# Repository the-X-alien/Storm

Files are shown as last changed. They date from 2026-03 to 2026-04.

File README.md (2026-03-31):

# Storm | A DIY 3D Printer



An open-source Cartesian bedslinger 3D printer built and designed from scratch to beat the Bambu Lab A1 in speed and print quality, by a 13 year old

Most budget 3D printers sacrifice speed for price or quality. Storm is better because it focuses on all three, fast, high quality, and affordability

I used a big Cartesian bedslinger structure + Klipper input shaping + high quality components.

## Goals
- 300–400mm/s print speeds, sub-5min Benchy
- Beat the Bambu Lab A1 in speed and quality
- Under $350 total including shipping and taxes
- Open source
- Screen
- Klipper Firmware
- Cool

## Specs
- Motion system: Cartesian bedslinger
- Build volume 220×220×300mm
- Firmware: Klipper
- Extruder: Sherpa Mini
- Hotend: TZ V6
- Probe: 3DTouch
- MCU: BTT SKR Mini E3 V3.0
- Raspberry Pi Zero 2W
- Display: ILI9341 2.8" SPI touchscreen
- Part Cooling: Dual 5015 blower fans 24V
- Hotend cooling: 4010 axial fan 24V
- Bed: 235×235mm 24V aluminum heated bed (Ender 3 bed) + PEI textured build plate

## Frame
- 4× 2040 aluminum extrusion 350mm for the base
- 2× 2020 aluminum extrusion 350mm for the Z towers
- 1× 2020 aluminum extrusion 350mm for the top crossbar

## Motion
- 8mm smooth linear rods on all axes (X, Y, Z) rails are too expensive :(
- LM8UU linear bearings
- T8 leadscrews 330mm for Z axis
- GT2 6mm belt for X and Y
  
## BOM
https://docs.google.com/spreadsheets/d/1btD1Bjle54Zft8ynW4hvl1bNV1Zsg6aF89J3ntGE-do/edit?usp=sharing

Total: ~$315 before tax and ~$347 with tax

## CAD
assembly in Onshape:
https://cad.onshape.com/documents/37467ea71eb1fca5838973f8/w/7266e1215341462849f7532b/e/d342240afd8f3da62d0e4bb2

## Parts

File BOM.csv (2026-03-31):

Part | Qty Needed | Total Cost | Why? | Anything Else? | Link
2040 T-slot extrusion 350mm | 4 | $27.00 | For base of the frame | Clear Anodize | HFS5-2040-350 | https://us.misumi-ec.com/vona2/detail/110302684350/?HissuCode=HFS5-2040-350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
2020 T-slot extrusion 350mm | 3 | $17.31 | For the X Axis and the two Z towers | Clear Anodize | HFS5-2020-350 | https://us.misumi-ec.com/vona2/detail/110302683830/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
M5 T-Nut Kit | 1 | $4.92 | To join parts | It has 100Pcs | https://www.aliexpress.us/item/3256808597854176.html?curPageLogUid=Rnu7snFro4kU
M5 8mm Bolt Kit | 1 | $4.99 | To screw into the T Nuts | It has 100Pcs | https://www.amazon.com/Stainless-Threaded-Spanner-Furniture-Fixture/dp/B0FPG1VZYH?s=hi
8mm smooth rod 350mm | 6 | $28.74 | For Y Guiding For the Bed and For Z Guiding For the Linear Rail | 6Pcs 8mm x 350mm | https://www.aliexpress.us/item/3256807362660070.html?mp=1
LM8UU linear bearing | 12 | $6.32 | 2 per rod, slides along smooth rod | 10Pcs | https://www.amazon.com/Bearings-Diameter-Bushing-Engraving-Projects/dp/B0GCKMDYPG?s=bazaar&srs=121974693011
T8 leadscrew 330mm | 2 | $9.54 | For Z Movement for the Linear Rail | 2Pcs 330mm Lead 8mm with nut | https://www.aliexpress.us/item/3256805992640426.html?src=google
5mm to 8mm flexible shaft coupler | 2 | $3.94 | Z motor to leadscrew | 5mm x 8mm | https://www.aliexpress.us/item/3256807100994003.html?src=google
GT2 6mm open belt | 1 | $3.90 | To move X and Y | White 5M | https://www.aliexpress.us/item/3256805175395061.html?mp=1
20T GT2 pulley 5mm bore | 4 | $3.96 | On X and Y motor shafts | 20 Teeth 5mm | https://www.temu.com/goods.html?goods_id=601099817656513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
GT2 5mm smooth idler pulley | 4 | $6.78 | Belt routing and tensioning | 5Pcs 20T W6 B5 Without Teeth | https://www.aliexpress.us/item/3256806303110250.html?curPageLogUid=b8VNkbBWfE8c
Nema17 Stepper Motor 17HS4401 | 1 | $0.99 | Y |  | https://www.aliexpress.us/item/3256808273084374.html?mp=1
Nema 17 Stepper Motor 42HS34 | 3 | $17.88 | X, 2x Z |  | https://www.aliexpress.us/item/3256805095424554.html?mp=1
Sherpa Mini Extruder | 1 | $17.55 | Extruder |  | https://www.aliexpress.us/item/3256804374952371.html?src=google
TZ V6 Hotend | 1 | $7.46 | Hotend | TZ V6 | https://www.aliexpress.us/item/3256808497028944.html?curPageLogUid=79nhbArLE8BA
Dual 5015 Blower Fans | 2 | $4.79 | Fans | 2pcs 24v Sleeve 4500RPM | https://www.aliexpress.us/item/3256807420529511.html?mp=1
4010 Axial Fan | 1 | $3.84 | Fan |  | https://www.aliexpress.us/item/3256806505312112.html?curPageLogUid=f7DXmx63Z9Cv
PTFE tube 1m | 1 | $2.35 | Filament Tube | 1m | https://www.aliexpress.us/item/3256807604679758.html?curPageLogUid=zfQeqruhbkQQ
Heated Bed | 1 | $21.59 | 235mm Heated Bed |  | https://www.amazon.com/Ender-V2-Heated-Bed-Replacement/dp/B08VHTW8CQ
235mm PEI Build Plate | 1 | $7.94 | 235mm Build Plate |  | https://www.aliexpress.us/item/3256808391943560.html?curPageLogUid=n9RwhLDzKk6A
Silicone bed leveling mounts | 4 | $2.67 | Attaches Bed to Bed Carridge | 4pcs | https://www.aliexpress.us/item/3256809017739961.html?curPageLogUid=N3SoxEZlCpfR
BTT SKR MINI E3 V3.0 | 1 | $27.60 | MCU |  | https://www.aliexpress.us/item/3256808846534149.html?mp=1
3DTouch | 1 | $7.39 | 3D Touch |  | https://www.aliexpress.us/item/3256805422565595.html?mp=1
Raspberry Pi 0 2W | 1 | $0.00 | Running Klipper Firmware | I have one already
ILI9341 2.8" SPI touchscreen | 1 | $0.00 | Touchscreen to control the printer | I have one already
DC 24V 15A 360W PSU | 1 | $17.98 | Power Supply | 24V 15A 360W | https://www.amazon.com/gp/product/B0146IAXYO/ref=ewc_pr_img_1?smid=A3R1K2GDMNRTEL&psc=1
LM2596S DC-DC Buck Converter | 1 | $0.00 | Power Supply For the Pi | I have one already
ADXL345 accelerometer module | 1 | $0.00 | Input Shaping | I have one already
Mechanical endstop limit switch | 3 | $4.59 | To know the end of the axis |  | https://www.amazon.com/MXRS-Hinge-Momentary-Button-Switch/dp/B088W8WMTB?s=bazaar&srs=121974693011
20awg Silicone Electrical Wire Cable | 1 | $9.98 | Wires | 6 Colors, 20 AWG | https://www.amazon.com/Electrical-Gauge-Silicone-Cable-Black/dp/B08QVKJPZP?s=bazaar&srs=121974693011
16AWG silicone wire | 1 | $7.99 | Wires for the Bed |  | https://www.amazon.com/Silicone-Electrical-Cable%EF%BC%8810ft-Temperature-Resistant/dp/B0D93K21TN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
M3 Screws and Nuts Assortment | 1 | $7.20 | Screws for everything besides the frame and joints |  | https://www.amazon.com/Button-Socket-Assortment-Strength-Appliance/dp/B0F9Y9WQVV?s=bazaar&srs=121974693011
8MM M3 Screws | 1 | $4.76 | Because I will need more than the 20 in the kit |  | https://www.amazon.com/720pcs-Assorted-Plastic-Furniture-Machinery/dp/B0GCLG1ZYB?s=bazaar&srs=121974693011
M3 Heat Set Inserts | 1 | $4.13 | Heat Set Inserts |  | https://www.amazon.com/Threaded-Inserts-Embedment-Printing-Automotive/dp/B0DNVZPX2B?s=bazaar&srs=121974693011
Inlet Module Plug Socket | 1 | $6.29 | The power switch and adapter for the psu |  | https://www.amazon.com/button-Adapter-Connector-Socket-MXRS/dp/B082ZFRV1B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
NEMA 5-15P to IEC320 C13 Power Cord | 1 | $2.79 | To plug into the wall |  | https://www.amazon.com/Monoprice-Power-Cord-Monitors-Scanners/dp/B08TMFZTFZ
Filament | 1 | $9.99 | To test the printer |  | https://www.amazon.com/Filament-Printing-Dimensional-Accuracy-Beginners/dp/B0F66GQHQ9
TOTAL | 40 | $315.15 | $346.67

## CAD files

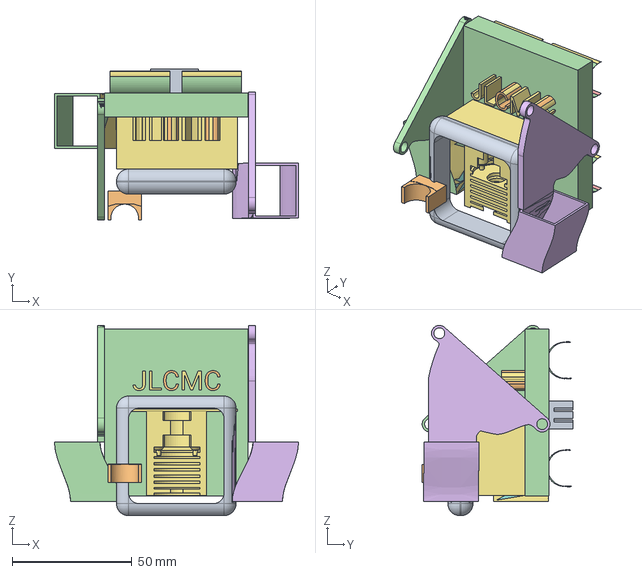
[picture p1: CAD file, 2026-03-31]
CAD/TOOLHEAD.step
102.0 x 63.1 x 79.6 mm

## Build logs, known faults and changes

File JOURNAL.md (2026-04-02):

Made by: @the-X-alien // Dhiaan Dave
Repository link: https://github.com/the-X-alien/Storm/
Total hours so far: 36

- [] I have a 3D printer or will be getting one before March 21st (printing legion pls save me)

---
### Status: Design Complete

---
### Goals:

- Beat the A1 at everything
- Cartesian bedslinger (like the Bambu Lab A1)
- 300×300×450mm build volume
- 500–700mm/s, sub-5min Benchy, high quality
- Screen, WiFi, Quiet
- Under $350 including shipping/taxes

---
### Day 1 - Feb 28 2026 - 2 Hours
I thought that Campfire SJ would be a good place to start making my printer because I was an org and not a participant.

But the second I opened the Infill website, I was lost by all the terms like Gantry, Toolhead, and Extrusions. 

But after googling and asking various AI chatbots, I learned that the Gantry is the frame system that allows movement, the toolhead is the part that encompasses the hotend and extruder, and extrusions are metal parts that make up the frame of a printer.

But I was still lost on how to actually make the 3D printer.

After watching a few YouTube videos on how to assemble the frame of a Cartesian 3D printer, I learned that the frame is built of a square base made from metal extrusions, and then there are two extrusions attached vertically on each side with one extrusion connecting them, allowing X Y and Z movement.

One video that really helped me was this one video on how the Bambu Lab A1 works, because it is also a Cartesian printer: https://www.youtube.com/watch?v=f94CnlQ0eq4

I understood the frame completely, but now I was lost on how to make things like the toolhead.



And right then, Alex (@alexren) pulled up to the event and I asked him for help.

He explained to me how he made his tool head by modeling the inside with the dimensions of the hotend, and how he added magnets to make the hotend hotswapable.
He also recommended that I look at other 3D printers to see what they did for their toolhead and other parts.

So I viewed printers like PandA and Nighthawk and saw their toolhead design.

And now I need to pick a hotend and an extruder so I can model my toolhead.

---
### Day 2 - Mar 3 2026 - 5 Hours

I spent some more time researching what parts I am actually using to build the 3D printer.

(to come up with this list, I had to read alot of reddit, watch many youtube videos, and I had to ask many questions to Claude and Grok)

So, I had to decide what kind of Aluminum extrusions to use.

I needed the frame to be both sturdy and impact resistant.

So, I had a large base made up of 4x 350mm 4040 Extrusions to spread vibration impact,

Then 2x 2040 Extrusions for the Z axis movement,

And the cross bar uptop will be a 2020 extrusion.

To connect them, I will be using cornerplates.

The extruder will be a Orbiter V2.5 which is the evolution of the V2.0 which is the standard lightweight direct-drive extruder for fast bedslingers

And the hotend will be a Trianglelab TZ V6 2.0 Hotend which is considered to be a budget A1 hotend, because it prints 30–45 mm³/s on PLA with a 0.6 mm nozzle compared to the A1's 20–25 mm³/s speed, and it has a bi-metal heatbreak, copper block, fast heating, and it is CHT-compatible nozzle options. It is also super  lightweight, reliable, and it will work with with most V6-style mounts. (V6 style mount to keep in mind when im cadding the toolhead)

For the nozzle, I'll go with any generic no name 0.4 mm hardened steel CHT-style (3-hole/high-flow) nozzle because 0.4mm is the industry standard for a balance of speed and quality for nice printers like the A1, A1 Mini, and Ender 3.

For cooling, I will get Dual 5015 blower fans with high static pressure (24V) because the nozzle and hotend are going to run hot, and so this powerful combination should cool it down.

For leveling, im using the Klicky probe, which is better than the CR Touch and the BL Touch in everysingle way of acuracy, weight, noise.

---
### Day 3 - Mar 4 2026 - 6 Hours (I didn't think research would take this long :heavysob:)

Made some modifications to the above parts list after reading more on Reddit

Aparently since the Klicky probe needs to dock, it's not ideal for bedslingers, and designed for other printers.
So instead, I am switching to the BTT Eddy, because it is super fast and scans the entire bed in one go, making my printing time faster.

Aparently CHT nozzles are a pain to clean if they get a clog and are annoying, and you might just have to throw them away altogether.
So I'll start with a basic standard hardened steel 0.4mm V6 nozzle because I'm a beginner and I want the printer to work before I start trying anything crazy.

Scratch the first thing, I'm going with a CR Touch because the the BTT Eddy is influenced by location and is aparently a pain to calibrate because it is super dependent on the magnetic field of the area.


Wait scratch that again, (I'm sorry) I'm trying to make my printer as fast as possible so a light probe would help, and the Biqu Microprobe is recomeneded because it only weighs 6 grams!


(I should put a disclaimer that I might change any parts later if I get recommendations or I find a problem with them)

I guess I should start with the motherboard, so for the control board, I am going with the BTT SKR Mini E3 V3, because not only is it super popular, but its also super cheap. It also just makes things simple.


Then for the brain, I am using a BTT Pi V1.2.1, because it is designed for the exact motherboard, it can run Klipper, and its optimized for printing. It also has an SPI Port

So I can connect a TFT35 SPI touchscreen for Klipperscreen so I can control the printer without an external screen.


For my motors, I am choosing the NEMA 17 Stepper Motors because they have high torque and good precision to have detailed 3D prints.


TO keep the thing running, my power supply will be a 24V 15A one, because all of my components take 24V to have more power.


For my heated base, I will be using a 310x310mm 24V 220W Aluminum Substrate Heated Bed, so my prints stick to the plate.


For the actual build plate, I will be using a 256x256mm PEI Textured buildplate because it is a good size so I can make most things, and the texture makes the print stick to the plate and also makes it easy to take off.


I also added a 24V 4010 Cooling fan to cool the toolhead because its going to get pretty hot.


I also added dual 24V 5015 Turbo Blowers to cool the plate and parts quickly.


I got all the electronics down, but I still need to find the extrusions and rails/rods, and I might have to change some parts because the total is already around $280.

---
### Day 4 - Mar 7 2026 - 3 Hours
After looking at my parts and looking at the prices, I started to question if this is actually possible

And the math said no

So I had to build the entire thing for cheaper

So I started swapping expensive parts for cheaper ones

So this isn't finalized (if you haven't realised I'm updating this as I go), but

I'm switching the BTT SKR Mini E3 V3.0 to the MKS Robin Nano V3 because it has a better chip and more ram so its faster, but it has less support in places like Reddit.

I'm switching the Orbiter V2.5 to the Sherpa Mini cause the orbiter is super expensive, and the Sherpa Mini is just lighter which makes my printer fast, and since it weighs less, its easier to stop making my prints more accurate (yay! paying attention in science class paid off!)

I also switched the BTT Pi with a normal Raspberry Pi Zero 2 W because the BTT PI is just a waste of money

I'm also going to find a cheaper smaller touch screen

And for thing like the hotend and nozzle, I'm gonna use clones that are just as good as the original instead of paying more

Everything else is going to stay pretty much the same, but even with this new budget, I'm pretty cooked

So I was wondering, how do I further lower the cost,

So I read other journals of people who made 3D printers last year and their BOMs (of course I did realize that tarrifs changed the  prices by alot for things)

And in one journal, I read that someone got sponsored by Polymaker

And that got me think about all the videos about making 3D printers that are sponsored by PCBWay, Polymaker, and tons of other 3D printing companies

So I spent some time making a list of all the companies that are in the 3D printing field and have sponsored projects before, or are just a big name in the business

I'll post the full link of sponsors here later, because I don't want them to get spammed before I send in my request : 


Now, I've finally decided to start working on the formal BOM on a spreadsheet to actually see what parts I need to swap and where the money is going (right now I'm just doing it in my head)

The link is: https://docs.google.com/spreadsheets/d/1btD1Bjle54Zft8ynW4hvl1bNV1Zsg6aF89J3ntGE-do/edit?usp=sharing

After checking the BOM from the one video, I watched earlier (https://www.youtube.com/watch?v=EX62plOF-So&list=PLyYZUiBHD1QjaYx7eCEW8zXvsgwEbAykY)

I learned that a site called Misumi has Extrusions for really cheap, so I'm getting all my extrusions from there

But, Aliexpress claims to be cheaper, but I'd have to have a talk with a seller

---
### Day 5 - Mar 9 2026 - 2 Hours
I started working on the BOM, and I planned out the full frame, and motion system



Now all thats left is the electronics

It was a bit challenging because I had to balance price, preformance, and shipping date for each part

I'm starting to wonder what sourcing parts was like before tarrifs and inflation

Because all the videos and articles I find are from years ago, when everything was cheap and you could make a high end 3D printer for $350

These days Extrusions are $60 alone

How did metal become so expensive?

But, since the Corner Plates were just too expensive, I'm going to try to just 3D print them

I realised, that I can probably print alot of the parts

I wonder if I can just print Extrusions . . .

Today we also had a group agreement to name all of our printers after real names, like Tim, David, John, Bruce, and I'm naming mine Bob.

It's going to be a play on Bob the Builder, so Bob the Printer

Tommorow, I plan on finishing the BOM and starting the toolhead design

Then on Thursday, I want to build the full CAD Assembly

And I hope that I can submit on friday, so I can order parts in time

---
### Day 6 - Mar 10 2026 - 2 Hours
Today I finshed the BOM, while keeping it under $350

But I had to make some sacrifices along the way ...

First, on a happier note, I discovered Amazon Haul after checking some other people's BOMs

And often, I found that for my parts, haul was cheaper!

For things like the endstops, the bearings, wire, etc

Anyways, one of the big changes I had to make was the extrusions

Since bigger extrusions cost more, I had to ditch the 4040s

So now, I was using 2040s for the base

2020s for the Z towers

And a 2020 for the crossbar

Other changes:

I went back to the BTT SKR E3 V3 Mini, because the other one doesn't have drivers for the motors with it, so its an additional cost

Next, instead of using a Nema17 Stepper Motor 17HS4401 for all the axes, I'm only using it for the Y axis

And for the Z and X axis, I am using two Nema 17 Stepper Motor 42HS34

Unfortunately, 300mm heated beds are really hard to find, but every site had tons of Ender 3 beds, so now my bed is 235mm

Then for the probe, I went with the absolute cheapest, the 3DTouch

Next, instead of buying a new touchscreen, I am using a ILI9341 2.8" SPI touchscreen that I have lying around

Finally, I switched all the linear rails to linear rods because they are so much more cheaper

I also emailed JLCMC for sponsorship because they have about half of the things I need, from the extrusions to the motors

---
### Day 7 - Mar 15 2026 - 6 Hours

Finally, I decided to address the Elephant in the room, the toolhead

I put this off the whole week because I had a bunch of schoolwork and a science olympaid tournament, but I mostly put it off because I am quite inexperienced at CAD and designing a whole toolhead looked scary

So finally facing it, I had to make the toolhead

And I started off by thinking of the most simple way to make it, which was to carve out each part from a block and then join all the blocks together so I can just insert all the parts

So I did that, but I had no idea how

I started off by figuring out how to import a part

And that looked simple, just press the import button

But, the immports are all in different tabs, so you have to make an Assembly and then insert the imports

But you can't create a sketch in an assembly, so then you had to make a part studio in the assembly's context

That wasn't the end though, you then had to use the transform function to copy the part to the part studio

And that was all to just get the part

To carve it, I initally thought I could just use the remove feature of the extrude function, but thats not how parts work

So I had to learn all about the "boolean" function, which can preform union, subtraction, and intersection operations

Merging, carving, or intersecting parts

So using that function, I had to select the part as the "tool" and then a block as the "target" and then it would carve the shape of the part into the block

So, following this video, I learned all the sections I had to make and I got started: https://www.youtube.com/watch?v=6OJSKmMlmZA

Hotend mount: 



Fan holder:



3DTouch holder:



X Carriage:



Then I had to do something different for the fan ducts, because you can't just carve that

I had to use this video: https://youtu.be/o-jrtvJ98nE



And the loft function to make the duct for the fan to slide into

Finally, I opened an Assemmbly and inserted all the parts and put it together

When it was done, it looked like this:





Very Makeshift, but functional. (in theory)

---
### Day 8 - Mar 28 2026 - 2 Hours

I now had to address the other Elephant in the room, the actual whole assembly

And since my homework was light this weekend and Monday was a holiday, I was determined to finished by the end of the long weekend

So I had to think the entire thing through

How was I going to do this

I figured out that I would have the 2040s face up with the 40mm side up to mimic a 4040 extrusion

And I would connect everything with a 2020 corner bracket

I had to learn how to source parts, and usually, my best bet was GrabCAD because they had nice Step files of almost everything

By the end of the day, I had this:



Again, I'm not that good at CAD, so even this took me a while

---
### Day 9 - Mar 29 2026 - 4 Hours

Today I had to lock in

Since I'm still a beginner to 3D printers, I didn't know how to assemble the whole thing and the motion systems

So I referenced this youtube series a bunch of times, step by step to assemble it, and I also borrowed a bunch of the 3D parts they used for things like motor mounts, tensioners, and various other pieces: https://www.youtube.com/watch?v=EX62plOF-So&list=PLyYZUiBHD1QjaYx7eCEW8zXvsgwEbAykY

And by diving into various cad sites like GrabCAD, TraceParts, and Cult 3D, I found the parts I needed to assemble it

The hardest thing to find was the Y Carriage for an Ender 3 bed, because there wearn't that many and the ones that were there used the Ender 3's motion system and not rails

Luckily I found a good carriage and then for attaching to the bearings, I found a seperate block to fit onto the carriage

All the other parts were also a headache to find, but they were easier than this

For most of the parts that would attach to the extrusions, I took from the videos, but I often had to modify them or find a different one because my printer was different

I completed the entire process while doomscrolling, listening to music, playing fortnite, and eating

At the end, I had this: 



The entire Y and Z axis movements done, and the X carriage attached to the linear rods

---
### Day 10 - Mar 30 2026 - 4 Hours

A big one! Day 10 and the 30th of March!

Today was the day I finished!

I assembled the X movement, all the electronics, and double checked everything

For the X movement I initally made the spacing between the bearing holder on the carriage random, so the rods didn't fit right with the parts on the end

So I had to redesign the X carriage properly

Then I added all of the parts onto the toolhead like the extruder, hotend, fans, probe

Then I had to place all of the other electronics like the PSU, MCU, and the screen

So found holders for all those parts and a case for the screen, in which I fit the Raspberry Pi Zero 2W

After double checking, I forgot the T connector that connects the 2020 to the 2040 Z towers, but I quickly added it

The final assembly looks like this:



And the link to it is https://cad.onshape.com/documents/37467ea71eb1fca5838973f8/w/7266e1215341462849f7532b/e/d342240afd8f3da62d0e4bb2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

Now, I'm current writing the Journal and I'm done with that, so I just have to do the README

---

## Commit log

2026-03-02 Revise JOURNAL.md with new hours and toolhead info
    Updated total hours and added details about toolhead assembly.
2026-03-03 Update JOURNAL.md with 3D printer assembly insights
    Added a helpful video link on the Bambu Lab A1 Cartesian printer and noted the need to choose a hotend and extruder for modeling the toolhead.
2026-03-03 Update JOURNAL.md with toolhead design insights
    Added an image and details about toolhead design discussions.
2026-03-04 Revise JOURNAL.md with new hours and goals
    Updated total hours and added detailed goals and progress for building a 3D printer, including parts selection and specifications.
2026-03-04 Revise parts list and probe selection for printer
    Updated parts list and switched to BTT Eddy probe for better performance. Added notes on CHT nozzles and choice of standard hardened steel nozzle.
2026-03-05 Revise 3D printer parts list and specifications
    Updated parts list and specifications for the 3D printer project, including changes to probes, nozzles, control board, and other components.
2026-03-08 Update JOURNAL.md with Day 1 build details
    Documented Day 1 progress on 3D printer build, including part substitutions for cost reduction and sponsorship exploration.
2026-03-10 Update total hours and add Day 5 journal entry
    Updated total hours and added entry for Day 5 detailing progress on the BOM and frame planning.
2026-03-31 Update JOURNAL with Day 6 progress and BOM changes
    Documented changes made to the BOM and component selections for the project, including part substitutions and cost-saving measures.
2026-03-31 Update JOURNAL.md with Days 7 to 10 entries
    Documented progress on toolhead assembly and CAD design.
2026-03-31 Rename Storm _ 3D printer _ BOM - Sheet1.csv to BOM.csv
    [BOM.csv]
2026-03-31 Update README with project details and specifications
    Added detailed project description, goals, specifications, frame, motion, bill of materials, and CAD links for the Storm 3D printer.
